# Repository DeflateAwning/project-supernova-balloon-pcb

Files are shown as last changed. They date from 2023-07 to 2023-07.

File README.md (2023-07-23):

# Project Supernova
A Helium Balloon, to assess the Helium Network.

## Features
This project is a PCB which is capable of being the primary payload on a PCB aboard a stratospheric helium balloon. The PCB intends to downlink 

* Onboard GPS for position tracking
* Atmospheric condition sensors (temperature/pressure/humidity) to generate downlink data
* Onboard PID-controlled heater and battery management
* Very low cost (<$100)

## Notes
* 3v3 regulated voltage. 9v unregulated battery voltage.
 
## Rev 2 Errata
1. Nothing yet (fingers crossed)

## Rev 1 Errata
1. DHT22 doesn't support 3V3 supply, technically
2. ADC2 doesn't work when wifi is enabled
3. DHT22 cannot be connected to pin D12, as D12 must be floating at boot
4. D34-D39 are input-only (so `TEMP_V+` is a problem)
5. LM335 onboard temperature sensor is basically incompatible with 3V3 systems
6. DHT22 needs a 10k pull-up to 3V3
7. RTF switch needs resistors on each leg to prevent shorting in case of a make-before-break switch.
8. The voltage regulator footprint could use the pads moved a bit (and could include through-hole pins).
9. Should've added a pull-down resistor to the heater MOSFET to prevent heating during boot.
10. Shouldn't have put a via in the pad on the MOSFET, as it prevented the gate from soldering right, then burned the MOSFET when it entered the linear region. Should've used way larger pads on the hand-soldered SOT-23 MOSFET.

### Changes made to correct errata items (Rev 1.1)
* DHT22 (`DHT_DATA`) now connected to D23 (per Errata #3).
* DHT22 now has a 10k pull-up to 3V3 (Errata #6).
* `TEMP_V+` now connected to D25 (per Errata #4), and still left connected to D35.
* LM335 onboard temperature sensor is unused.

### OFIs
* Add LED on HEATER_EN net
* Add LED polarity on silk screen
* Consider 10u cap from GND to EN for programming
* D2 is the onboard LED, so probably best to not use it
* Should have referenced this doc: https://randomnerdtutorials.com/esp32-pinout-reference-gpios/
* Add jumper to disconnect power from GPS (because it uses so much power)

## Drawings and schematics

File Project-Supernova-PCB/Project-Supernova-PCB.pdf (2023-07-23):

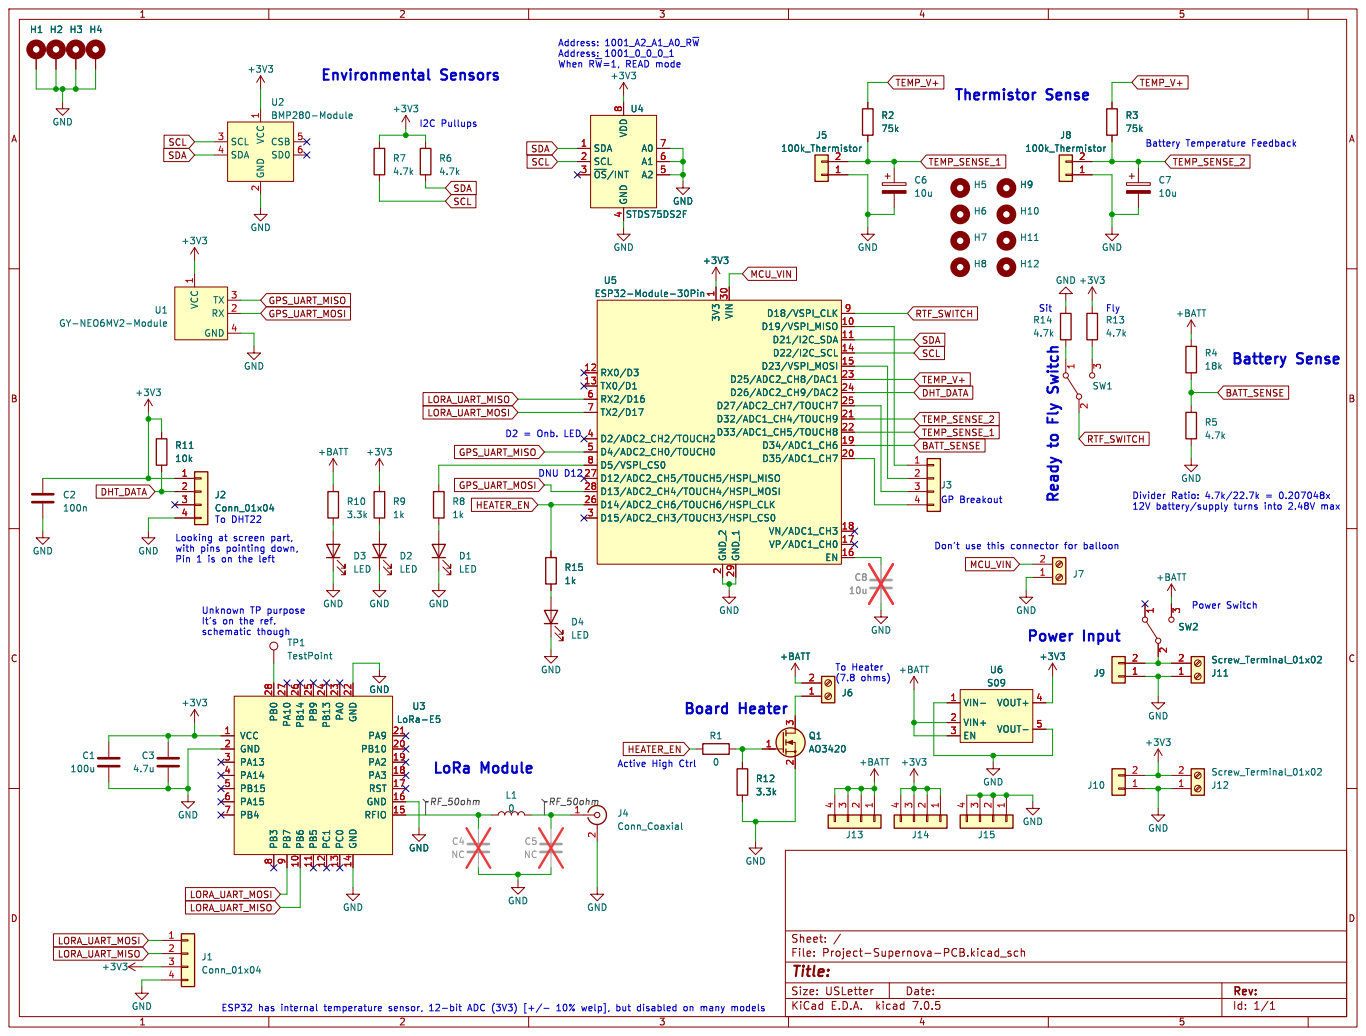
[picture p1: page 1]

Address: 1001_A2_A1_A0_R~{W} Address: 1001_0_0_0_1 When R~{W}=1,READ mode

2 SCL 3 SDA 4 CSB 5 SD0 6 U2BMP280-Module VCC

1 RX 2 TX 3 GND 4 U1 GY-NEO6MV2-Module +3V3

2 D35/ADC1_CH7 20 D32/ADC1_CH4/TOUCH9 21 D33/ADC1_CH5/TOUCH8 22 D25/ADC2_CH8/DAC1 23 D26/ADC2_CH9/DAC2 24 D27/ADC2_CH7/TOUCH7 25 D14/ADC2_CH6/TOUCH6/HSPI_CLK 26 D12/ADC2_CH5/TOUCH5/HSPI_MISO 27 D13/ADC2_CH4/TOUCH4/HSPI_MOSI 28 GND_1 29 D15/ADC2_CH3/TOUCH3/HSPI_CS0 3 VIN 30 D2/ADC2_CH2/TOUCH2 4 D4/ADC2_CH0/TOUCH0 5 RX2/D16 6 TX2/D17 7 D5/VSPI_CS0 8 D18/VSPI_CLK 9 U5 ESP32-Module-30Pin GND GND GND

(7.8 ohms) Unknown TP purpose

Active High Ctrl Board Heater

Id: 1/1 Title: File: Project-Supernova-PCB.kicad_sch Sheet: /

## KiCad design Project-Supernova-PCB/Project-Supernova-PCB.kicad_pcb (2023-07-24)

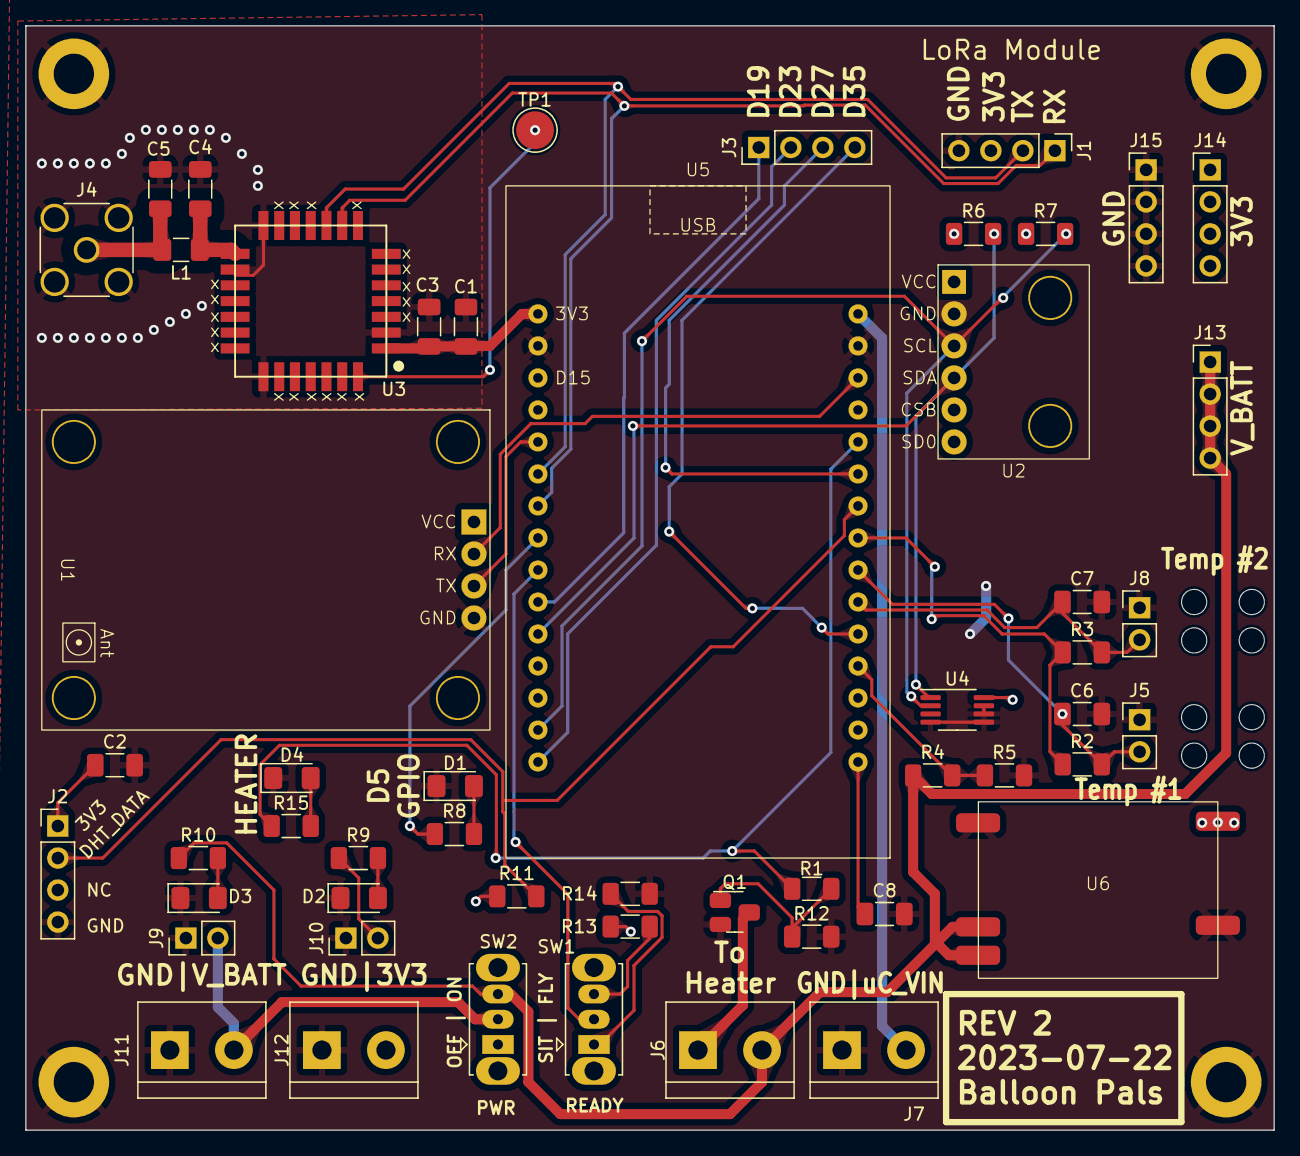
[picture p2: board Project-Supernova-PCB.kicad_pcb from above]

Board: 2 copper layers, 99.1 x 87.6 mm, 65 parts (0 on the bottom side), 35 nets.

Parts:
C1: 100u; C_1206_3216Metric_Pad1.33x1.80mm_HandSolder
C2: 100n; C_1206_3216Metric_Pad1.33x1.80mm_HandSolder
C3: 4.7u; C_1206_3216Metric_Pad1.33x1.80mm_HandSolder
C4, C5: NC; C_1206_3216Metric_Pad1.33x1.80mm_HandSolder
C6, C7, C8: 10u; C_1206_3216Metric_Pad1.33x1.80mm_HandSolder
D1, D2, D3, D4: LED; LED_1206_3216Metric_Pad1.42x1.75mm_HandSolder
H1, H2, H3, H4: MountingHole_Pad; MountingHole_3.2mm_M3_DIN965_Pad
H5, H6, H7, H8, H9, H10, H11, H12: MountingHole; MountingHole_2mm
J1, J2, J3, J13, J14, J15: Conn_01x04; PinHeader_1x04_P2.54mm_Vertical
J4: Conn_Coaxial; SMA_Wurth_60312002114503_Vertical
J5, J8: 100k_Thermistor; PinHeader_1x02_P2.54mm_Vertical
J6, J7, J11, J12: Screw_Terminal_01x02; TerminalBlock_bornier-2_P5.08mm
J9, J10: Conn_01x02; PinHeader_1x02_P2.54mm_Vertical
L1: 0; L_1206_3216Metric_Pad1.42x1.75mm_HandSolder
Q1: AO3420; SOT-23-MassivePads-HandSolder
R1: 0; R_1206_3216Metric_Pad1.30x1.75mm_HandSolder
R2, R3: 75k; R_1206_3216Metric_Pad1.30x1.75mm_HandSolder
R4: 18k; R_1206_3216Metric_Pad1.30x1.75mm_HandSolder
R5, R6, R7, R13, R14: 4.7k; R_1206_3216Metric_Pad1.30x1.75mm_HandSolder
R8, R9, R15: 1k; R_1206_3216Metric_Pad1.30x1.75mm_HandSolder
R10, R12: 3.3k; R_1206_3216Metric_Pad1.30x1.75mm_HandSolder
R11: 10k; R_1206_3216Metric_Pad1.30x1.75mm_HandSolder
SW1, SW2: SW_SPDT; SW_Slide_1P2T_CK_OS102011MS2Q
TP1: TestPoint; TestPoint_Pad_D3.0mm
U1: GY-NEO6MV2-Module
U2: BMP280-Module
U3: LoRa-E5; LoRa-E5_HandSolder
U4: STDS75DS2F; MSOP-8_3x3mm_P0.65mm
U5: ESP32-Module-30Pin
U6: S09

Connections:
+3V3: C1.1, C2.1, C3.1, J1.3, J2.1, J10.2, J12.2, J14.1, J14.2, J14.3, J14.4, R6.1, R7.1, R9.1, R11.1, R13.1, U1.1 (VCC), U2.1 (VCC), U3.1 (VCC), U4.8 (VDD), U5.1 (3V3), U6.4 (VOUT+)
+BATT: J6.2, J13.1, J13.2, J13.3, J13.4, R4.1, R10.1, SW2.3 (C), U6.2 (VIN+), U6.3 (EN)
BATT_SENSE: R4.2, R5.1, U5.19 (D34/ADC1_CH6)
DHT_DATA: J2.2, R11.2, U5.24 (D26/ADC2_CH9/DAC2)
GND: C1.2, C2.2, C3.2, C4.2, C5.2, C6.2, C7.2, C8.2, D1.1 (K), D2.1 (K), D3.1 (K), D4.1 (K), H1.1, H2.1, H3.1, H4.1, J1.4, J2.4, J4.2 (Ext), J5.1, J7.1, J8.1, J9.1, J10.1, J11.1, J12.1, J15.1, J15.2, J15.3, J15.4, Q1.2 (S), R5.2, R12.2, R14.2, U1.4 (GND), U2.2 (GND), U3.2 (GND), U3.14 (GND), U3.16 (GND), U3.22 (GND), U4.4 (GND), U4.5 (A2), U4.6 (A1), U4.7 (A0), U5.2 (GND_2), U5.29 (GND_1), U6.1 (VIN-), U6.5 (VOUT-)
GPS_UART_MISO: U1.3 (TX), U5.5 (D4/ADC2_CH0/TOUCH0)
GPS_UART_MOSI: U1.2 (RX), U5.28 (D13/ADC2_CH4/TOUCH4/HSPI_MOSI)
HEATER_EN: R1.1, R15.1, U5.26 (D14/ADC2_CH6/TOUCH6/HSPI_CLK)
LORA_UART_MISO: J1.2, U3.10 (PB6), U5.6 (RX2/D16)
LORA_UART_MOSI: J1.1, U3.9 (PB7), U5.7 (TX2/D17)
MCU_VIN: J7.2, U5.30 (VIN)
unnamed: D1.2 (A), R8.2
unnamed: D2.2 (A), R9.2
unnamed: D3.2 (A), R10.2
unnamed: D4.2 (A), R15.2
unnamed: J3.1, U5.10 (D19/VSPI_MISO)
unnamed: J3.2, U5.15 (D23/VSPI_MOSI)
unnamed: J3.3, U5.25 (D27/ADC2_CH7/TOUCH7)
unnamed: J3.4, U5.20 (D35/ADC1_CH7)
unnamed: C5.1, J4.1 (In), L1.2
unnamed: J6.1, Q1.3 (D)
unnamed: J9.2, J11.2, SW2.2 (B)
unnamed: Q1.1 (G), R1.2, R12.1
unnamed: R14.1, SW1.1 (A)
unnamed: R13.2, SW1.3 (C)
unnamed: TP1.1, U3.28 (PB0)
unnamed: C4.1, L1.1, U3.15 (RFIO)
unnamed: R8.1, U5.8 (D5/VSPI_CS0)
unnamed: C8.1, U5.16 (EN)
RTF_SWITCH: SW1.2 (B), U5.9 (D18/VSPI_CLK)
SCL: R7.2, U2.3 (SCL), U4.2 (SCL), U5.14 (D22/I2C_SCL)
SDA: R6.2, U2.4 (SDA), U4.1 (SDA), U5.11 (D21/I2C_SDA)
TEMP_SENSE_1: C6.1, J5.2, R2.2, U5.22 (D33/ADC1_CH5/TOUCH8)
TEMP_SENSE_2: C7.1, J8.2, R3.2, U5.21 (D32/ADC1_CH4/TOUCH9)
TEMP_V+: R2.1, R3.1, U5.23 (D25/ADC2_CH8/DAC1)

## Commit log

2023-04-09 Add GPS and BMP280 symbols and footprints
    [Project-Supernova-PCB.kicad_pcb, Project-Supernova-PCB.kicad_sch]
2023-04-10 Add more parts of schematic
    [Project-Supernova-PCB.kicad_sch]
2023-04-10 Update schematic docs, add TODO
    [Project-Supernova-PCB.kicad_sch]
2023-04-24 Add S09 symbol and footprint
2023-04-26 Add ESP32 microcontroller
    [Project-Supernova-PCB.kicad_pcb, Project-Supernova-PCB.kicad_sch]
2023-04-26 Add better LoRa footprint and better ESP symbol
    [Project-Supernova-PCB.kicad_sch]
2023-04-29 More work
    [Project-Supernova-PCB.kicad_pcb, Project-Supernova-PCB.kicad_sch]
2023-05-18 Plot latest schematic
2023-05-20 Connected MCU pins
    [Project-Supernova-PCB.kicad_sch]
2023-05-20 Lay out PCB
    [Project-Supernova-PCB.kicad_pcb, Project-Supernova-PCB.kicad_sch]
2023-05-20 Routed PCB
    [Project-Supernova-PCB.kicad_pcb, Project-Supernova-PCB.kicad_sch]
2023-05-20 Gerbers and such
    [Project-Supernova-PCB-B_Cu.gbl, Project-Supernova-PCB-B_Mask.gbs, Project-Supernova-PCB-B_Paste.gbp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]
2023-05-21 PCB changes, finish Rev1 as ordered
    [Project-Supernova-PCB-B_Cu.gbl, Project-Supernova-PCB-B_Mask.gbs, Project-Supernova-PCB-B_Paste.gbp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]
2023-07-19 Add Rev1.1 hot fix notes
    [Project-Supernova-PCB.kicad_sch]
2023-07-19 Main Rev2 schematic changes
    [Project-Supernova-PCB.kicad_sch]
2023-07-23 Lock in Rev2 Gerber
    [Project-Supernova-PCB-B_Cu.gbl, Project-Supernova-PCB-B_Mask.gbs, Project-Supernova-PCB-B_Paste.gbp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]
2023-07-24 Fix DRC, republish V2
    [Project-Supernova-PCB-B_Cu.gbl, Project-Supernova-PCB-B_Mask.gbs, Project-Supernova-PCB-B_Paste.gbp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]
2023-07-24 Add teardrops in Gerber
    [Project-Supernova-PCB-B_Cu.gbl, Project-Supernova-PCB-B_Mask.gbs, Project-Supernova-PCB-B_Paste.gbp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]
2023-12-25 Clean up very messy schematic
    [LoRa_Module.kicad_sch, ModulesA.kicad_sch, Power.kicad_sch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]
2023-12-31 Update schematic page size
    [LoRa_Module.kicad_sch, ModulesA.kicad_sch, Power.kicad_sch]
